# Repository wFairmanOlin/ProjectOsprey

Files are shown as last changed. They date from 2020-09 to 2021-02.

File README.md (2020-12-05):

# Project Osprey
#### Daniel Connolly and William Fairman

A Fall 2020 Project

<p align="center">
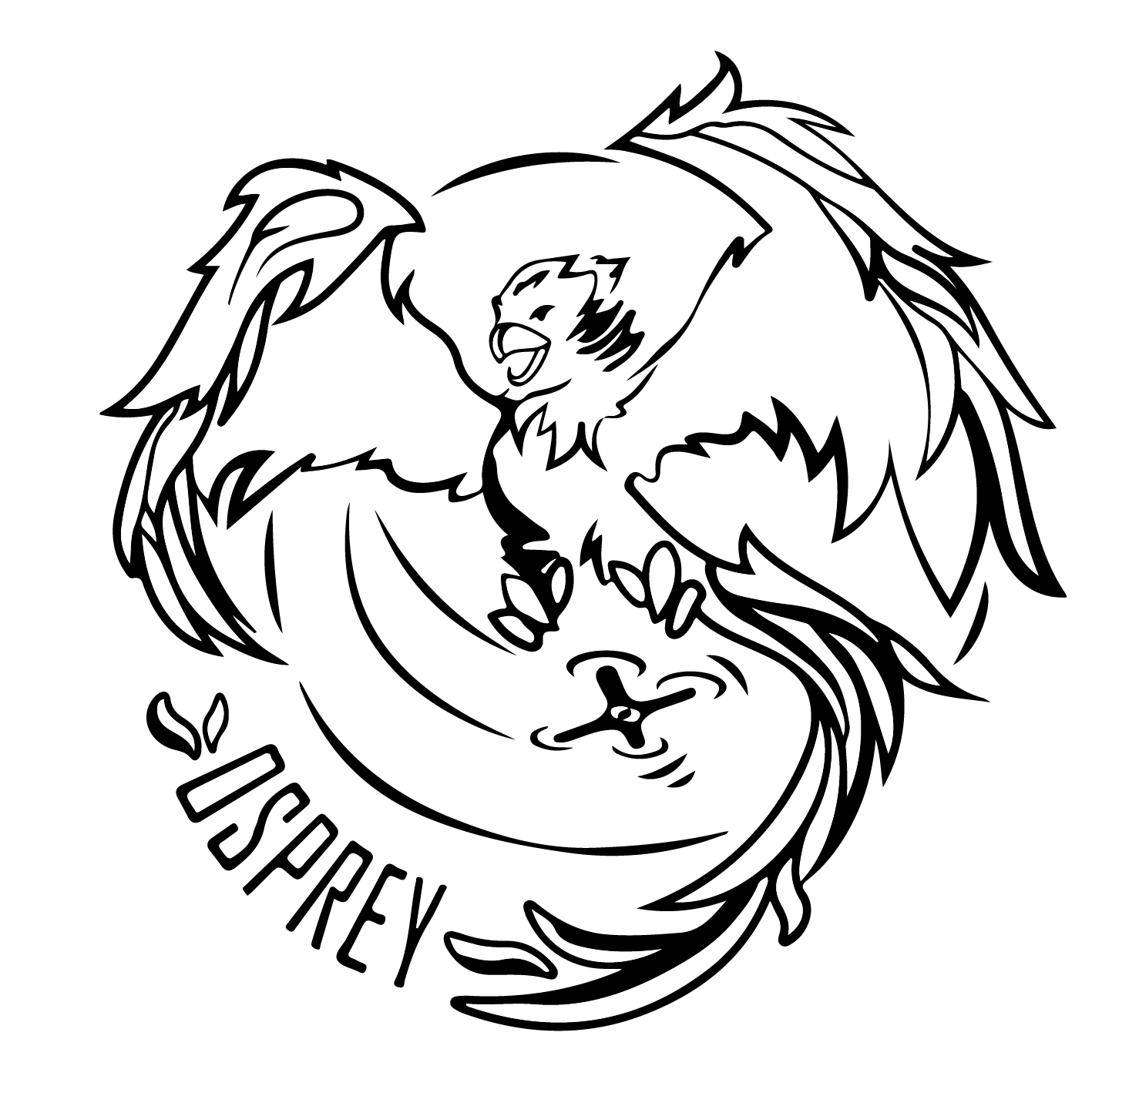
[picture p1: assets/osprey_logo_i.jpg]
Project Osprey

</p>
<p align="center">
<small>
<!--This logo is a modified version of work done by <a href="https://hweishin.carbonmade.com/">Hwei-Shin Harriman</a>, a fellow Olin student.--!>
  </small>
</p>

### Overview

We are developing a flight computer and drone as an exploration in electrical, mechanical, and firmware design.

### Subsystems

#### Electrical

Our flight computer is centered around the STM32F427VIT6 microcontroller. We have selected an IMU, barometer, GPS, and magnetometer to capture all of the necessary sensor data during flight. In addition, our board is equipped with a raspberry pi zero to which we intend to connect a small camera; the raspi communicates with the STM32 via I2C. We are also including a variety of connectors based off the [pixhawk design standard](https://github.com/pixhawk/Pixhawk-Standards/blob/master/DS-009%20Pixhawk%20Connector%20Standard.pdf) in order to connect to a variety of radios (FrSky, Spektrum, telemetry modules, etc). In order to be compatible with PX4 software, our computer also contains a microSD slot and on-board flash storage. Finally, we have created a power management system based around a TI buck converter that steps down battery voltage (12-25V) to 5V. Additional low-dropout regulators have been added to provided noise-free 3V3 to the sensors, STM, and radio modules. 

Besides providing basic computer vision, we are intending on utilizing the wifi chip on the raspi to stream video over a local network.

##### PCB Design
We have designed the first revision of our flight computer using Kicad and are currently waiting for fabrication and assembly from PCBWay. The board is 4 layers (Signal, GND, VCC, Signal) and contains roughly 120 surface mounted components. The minimnum trace/spacing width is 10/10mil.

![pcb_3d_view](assets/pcb_3d_view.png)

We have already been thinking about a revision 2! Heres what might be in the pipeline:
1. Onboard 2.4ghz radio (with a pcb antennae)
2. Replacing raspi with STM32H-series chip (embedded neural nets)
3. Faster primary micro-controller
4. Shrinking layout by replacing 0805 footprints with 0603 or smaller.

#### Mechanical

We are creating a 3-D printable chassis for our drone in AutoDesk's Fusion 360. At the moment, we are experimenting with Fusion 360's generative design features and how well these designs perform when 3-D printed as well as creating the basic chassis layout.

#### Firmware / Software

While we have not yet begun firmware / software development, we intend to start once we have shipped version 1 of our PCB. We expect to work in C++/C while developing for the STM32 as well as Python as we develop software on the raspberry pi.

### Goals

Our overarching goal for this project is to develop a drone capable of autonomous or semi-autonomous flight. In pursuit of this goal, we hope to advance our skills in the following areas:

1. Electrical design & PCB layout: This entails selecting the mcu, sensors, power management systems, and all supporting hardware as well as continuing to develop our KiCad knowledge.

2. Firmware development: We intend to learn C++ and advance our knowledge of firmware.

3. Computer vision: We have equipped our system with a raspberry pi with the intention of connecting a camera for basic computer vision processing.

4. Mechanical design: Taking high-level constraints about lift and drone layout into consideration, we intend to extend our CAD abilities.

Like the logo? This logo is a modified version of work done by [Hwei-Shin Harriman](https://hweishin.carbonmade.com/), a fellow Olin student.

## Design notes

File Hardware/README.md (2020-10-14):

# Project Osprey Electrical Hardware

We are designing a PCB in KiCad centered around an STM32 microcontroller for our flight computer.

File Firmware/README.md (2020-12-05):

# Project Osprey Firmware

We intend for our drone to fly semi-autonomously.

### TO DO:

- Look into Docker containerization of development environment
- Setup QGroundControl for use with our sensors
- Read through PX4 Firmware code
- Setup JMavSim and/or Gazebo for simulation

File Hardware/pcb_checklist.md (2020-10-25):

# PCB Checklist

## Review Parts (for new parts)
1. Check physical dimensions of fooptrint against datasheet 
2. Ensure pin numbers are properly oriented
3. Check num of pins on footprint and part-schematic
4. Ensure cathode/anode pin number is same on the datasheet, part-schematic, and footprint

## Review Schematic
1. Make sure all labels are connected and spelled correctly
2. Check GND and VDD connections
3. Ensure connectors are properly wired
3. Run DRC

## Review Layout
1. Check min tracing/spacing and vias match manufacturing specs
2. Check for overlapping fills (proper priorities set)
3. Look for fill islands (unconnected fills)
4. Make sure all text on Front/Back is visible
5. Make sure revision num, date, and author are up to date
6. Run 3D viewer to verify silkscreen
7. Run DRC

## Review Gerber
1. Check gerber output location for older files
2. Check centroid/drill locaiton for older files
3. Import gerber and drill files into Gerber Viewer (KiCad)

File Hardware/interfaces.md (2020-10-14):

## Interfaces
- SWD/JTAG
- Power (px)
  1. VCC_5V
  2. VCC_5V
  3. BATT_CURRENT
  4. BATT_VOLTAGE
  5. GND
  6. GND
- Power (4in1 ESC)
  1. VBAT
  2. TLM
  2. GND
  3. BATT_CURRENT
  4. M1
  5. M2
  6. M3
  7. M4
- SBUS
  1. VCC_5V
  2. SBUS
  3. RSSI
  4. VCC_3V3
  5. GND
- Telemetry
  1. VCC_5V
  2. MCU_TX
  3. MCU_RX
  4. MCU_CTS
  5. MCU_RTS
- PWM
- USB

### Optional
- DCMI
- SPI
- UART & I2C
- CAN
- PPM

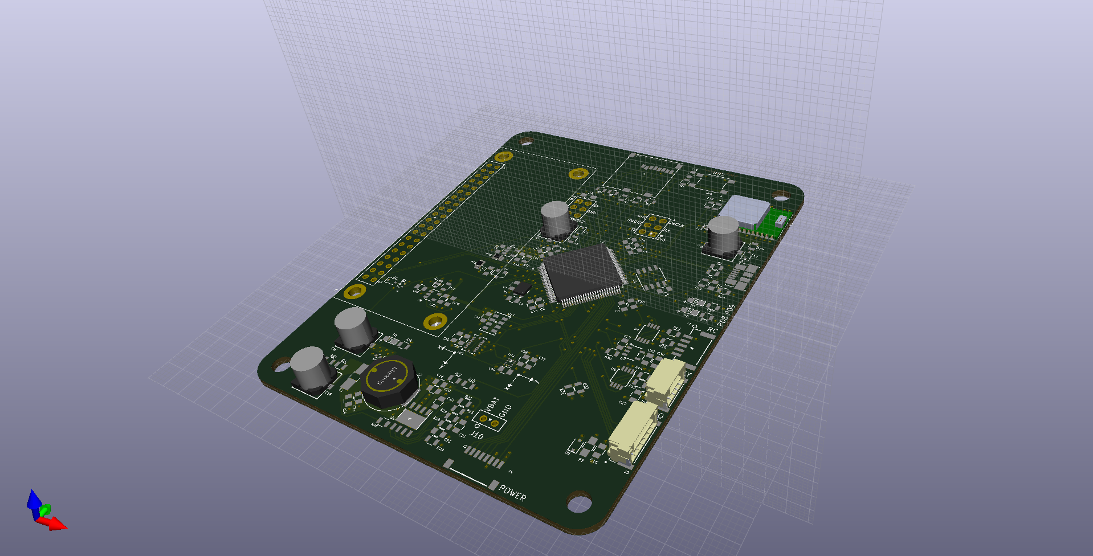
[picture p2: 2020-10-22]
Hardware/rev2/flight_computer/flight_computer.png

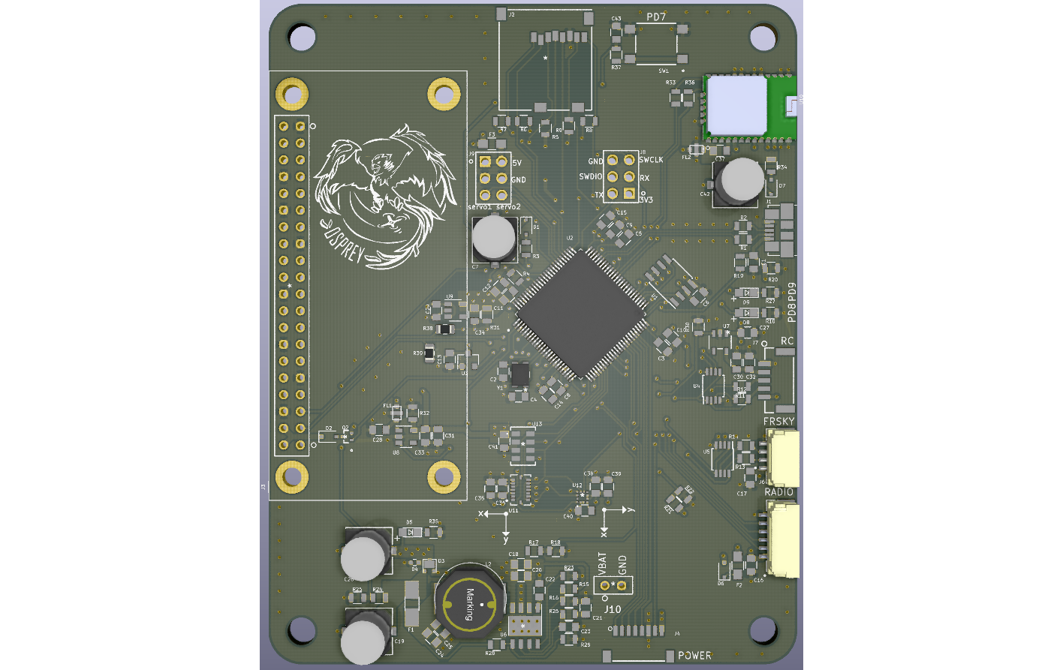
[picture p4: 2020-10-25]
assets/pcb_3d_view.png

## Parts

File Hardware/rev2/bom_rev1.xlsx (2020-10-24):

 |  |  | REV 1 BOM
Item # | *Designator | *Qty | Manufacturer | *Mfg Part # | Description / Value | *Package/Footprint | Type | Your Instructions / Notes
1 | C19, C26 | 2 | Rubycon | 10SGV100M6.3X6.1 | C_100u | SMD | SMD
2 | C21 | 1 | Murata Electronics | GRM2195C1H123GA01D | C_0u012 | 0805 | SMD
3 | C23 | 1 | Samsung Electro-Mechanics | CL21C121JDCNNNC | C_120P | 0805 | SMD
4 | C24, C25 | 2 | Taiyo Yuden | JMK212BJ476MG-T | C_47u | 0805 | SMD
5 | C37 | 1 | Murata Electronics | GRM21BR71C475KE51L | C_4u7 | 0805 | SMD
6 | C38 | 1 | KEMET | C0805C105Z4VACTU | C_1u | 0805 | SMD
7 | C4, C2 | 2 | Yageo | CC0805DRNPO9BN8R0 | C_8p | 0805 | SMD
8 | C43, C18, C34, C33, C27, C30 | 6 | Murata Electronics | GRM21BR61E106KA73K | C_10u | 0805 | SMD
9 | C6, C10, C11, C12, C14, C15, C13, C1, C20, C22, C31, C32, C36, C40, C39, C41, C35 | 17 | AVX Corporation | 08055C104JAT2A | C_0u1 | 0805 | SMD
10 | C7, C42 | 2 | Nichicon | UWT0G221MCL6GS | C_220u | SMD | SMD
11 | C9, C8, C3, C5, C16, C17, C29, C28 | 8 | TDK Corporation | CGB4B1X6S1C225K055AC | C_2u2 | 0805 | SMD
12 | D2, D1, D6, D7 | 4 | Nexperia USA Inc. | PMEG1030EJ,115 | D_Schottky_10V_3A | D_SOD-323F | SMD
13 | D3 | 1 | Nexperia USA Inc. | PMEG2020CPA,115 | D_Schottky_x2_20V | SOT1061 | SMD
14 | D4 | 1 | Littelfuse Inc. | PESD0402-140 | TVS_DIODE_14V | 0402 | SMD
15 | D8, D5 | 2 | OSRAM Opto Semiconductors Inc. | LG R971-KN-1 | LED_0805_Green | 0805 | SMD
16 | D9 | 1 | OSRAM Opto Semiconductors Inc. | LG R976-NR-1 | LED_0805_Red | 0805 | SMD
17 | F1 | 1 | Bel Fuse Inc. | 0ZCJ0200FF2C | PTC_6V_2A | 1206 | SMD
18 | F2, F3 | 2 | Bel Fuse Inc. | 0ZCK0050FF2E | PTC_6V_1A | 0805 | SMD
19 | FL1, FL2 | 2 | Murata Electronics | NFL21SP107X1C3D | EMI_Filter_CLC_100MHZ | SMD | SMD
20 | J1 | 1 | Molex | 473460001 | Micro_USB | SMD | SMD
21 | J10 | 1 | N/A | N/A | N/A | N/A | DNS | ignore part
22 | J2 | 1 | 3M | 2908-05WB-MG | MicroSD_molex | SMD | SMD
23 | J3 | 1 | N/A | N/A | N/A | N/A | DNS | ignore part
24 | J4 | 1 | JST Sales America Inc. | SM08B-SRSS-TB(LF)(SN) | JST_8_RA | SMD | SMD
25 | J5 | 1 | JST Sales America Inc. | SM06B-GHS-TB(LF)(SN) | JST_GH_6_RA | SMD | SMD
26 | J6 | 1 | JST Sales America Inc. | SM04B-GHS-TB(LF)(SN)- | JST_GH_4_RA | SMD | SMD
27 | J7 | 1 | JST Sales America Inc. | SM05B-GHS-TB(LF)(SN) | JST_GH_5_RA | SMD | SMD
28 | J8, J9 | 2 | Samtec Inc. | TSW-103-07-F-D | Conn_02x03 | through hole | through hole
29 | L2 | 1 | Würth Elektronik | 744066150 | L_15u | SMD | SMD
30 | Q2 | 1 | ON Semiconductor | NTA4151PT1G | PMOS_20V_.76A | SMD | SMD
31 | R1, R2 | 2 | Bourns Inc. | CR0805-FX-22R0ELF | R_22 | 0805 | SMD
32 | R10, R27 | 2 | Stackpole Electronics Inc | RMCF0805FT51R1 | R_51.1 | 0805 | SMD
33 | R12, R20 | 2 | TE Connectivity Passive Product | CRGCQ0805F470R | R_470 | 0805 | SMD
34 | R15, R31, R32, R25, R24, R36, R33 | 7 | Yageo | RC0805FR-07220RL | R_220 | 0805 | SMD
35 | R16 | 1 | Yageo | RC0805FR-0743K2L | R_43K2 | 0805 | SMD
36 | R17 | 1 | Yageo | RC0805FR-0769K8L | R_69K8 | 0805 | SMD
37 | R23 | 1 | Stackpole Electronics Inc | RMCF0805FT143K | R_143K | 0805 | SMD
38 | R26 | 1 | Stackpole Electronics Inc | RMCF0805FT3K74 | R_3K74 | 0805 | SMD
39 | R29 | 1 | Vishay Dale | CRCW080519K1FKEA | R_19K1 | 0805 | SMD
40 | R3, R13, R14, R34 | 4 | Yageo | RC0805JR-071KL | R_1K | 0805 | SMD
41 | R35 | 1 | TE Connectivity Passive Product | CRGCQ0805F120R | R_120 | 0805 | SMD
42 | R39, R38 | 2 | Yageo | RC0805FR-0710KL | R_10K | 0805 | SMD
43 | R4, R37, R11, R30, R19, R22, R21, R18 | 8 | Yageo | RC0805FR-07100KL | R_10K | 0805 | SMD
44 | R9, R8, R7, R6, R5, R28 | 6 | Stackpole Electronics Inc | RMCF0805JT68R0 | R_100K | 0805 | SMD
45 | SW1 | 1 | C&K | PTS645SM43SMTR92 LFS | Switch_SMT | SMD | SMD
46 | U1 | 1 | Cypress Semiconductor Corp | FM25V01A-G | FRAM_128K | SOIC-8 | SMD
47 | U10 | 1 | U-Blox | CAM-M8Q-0 | CAM-M8Q-0 | SMD | SMD
48 | U11 | 1 | Bosch Sensortec | BMI088 | BMI088 | SMD | SMD
49 | U12 | 1 | STMicroelectronics | LIS3MDLTR | LIS3MDLTR | SMD | SMD
50 | U13 | 1 | TE Connectivity Measurement Specialties | MS561101BA03-50 | Barometer | SMD | SMD
51 | U2 | 1 | STMicroelectronics | STM32F427VIT6 | STM32F427VITx | SMD | SMD
52 | U3 | 1 | Microchip Technology | MCP131T-300E/TT | MCP131T-300E_TT | SOT-23 | SMD
53 | U5, U4 | 2 | Nexperia USA Inc. | 74LVC2G86DP,125 | Dual_XOR_GATE | TSSOP-8 | SMD
54 | U6 | 1 | Texas Instruments | TPS54335ADDA | Buck_Converter_2 | SMD | SMD
55 | U7 | 1 | Diodes Incorporated | AP7365-33WG-7 | LDO_600MA | SOT-25_DIO | SMD
56 | U9, U8 | 2 | Texas Instruments | LP5907QMFX-3.3Q1 | LP5907QMFX-3.3 | SOT-23-5 | SMD
57 | Y1 | 1 | NDK America, Inc. | NX3225SA-24.000M-STD-CSR-1 | Crystal_24MHZ | SMD | SMD

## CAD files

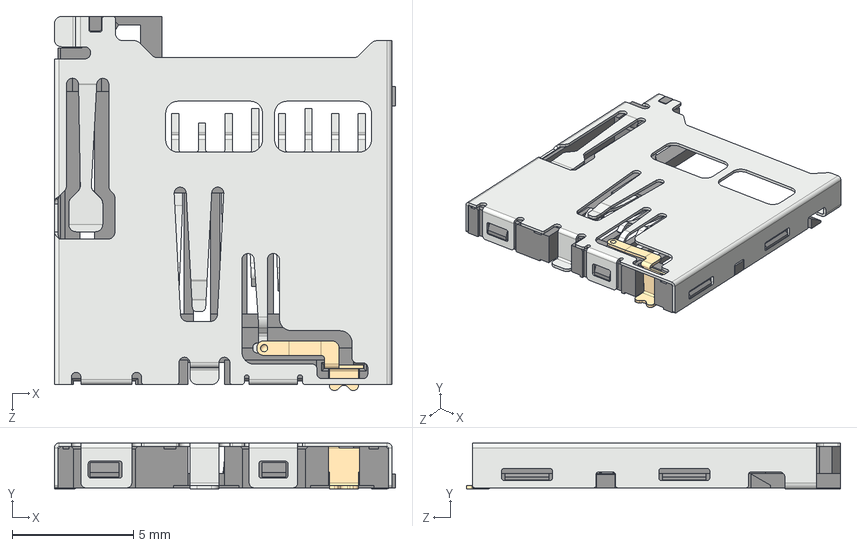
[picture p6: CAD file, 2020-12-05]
Hardware/3D_parts/micro SD Card Slot.step
14.1 x 1.90 x 15.5 mm
microSD_Body
microSD_Cover
microSD_Card_Detect
microSD_Pin_11.15 x 5
microSD_Pin_11.35 x 2
microSD_Pin_10.75

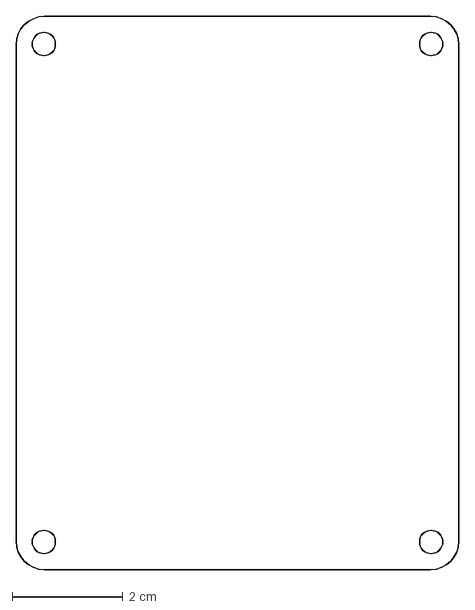
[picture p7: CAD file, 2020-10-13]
Hardware/rev2/flight_computer/circuitBoard v2.dxf
8.00 x 10.0 cm

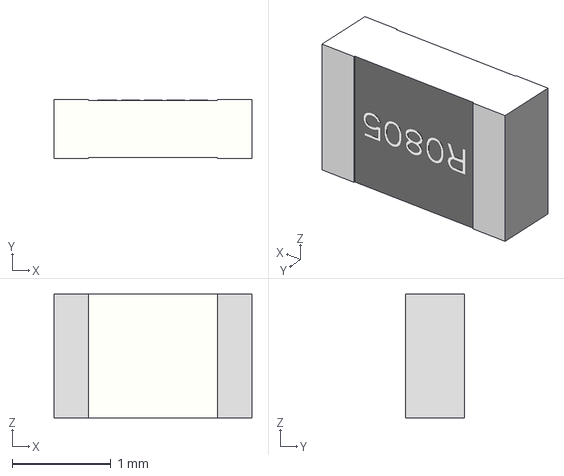
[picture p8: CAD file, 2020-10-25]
Hardware/3D_parts/rsmd-0805_l2_w1-25_h0-6.stp
2.00 x 0.6 x 1.25 mm

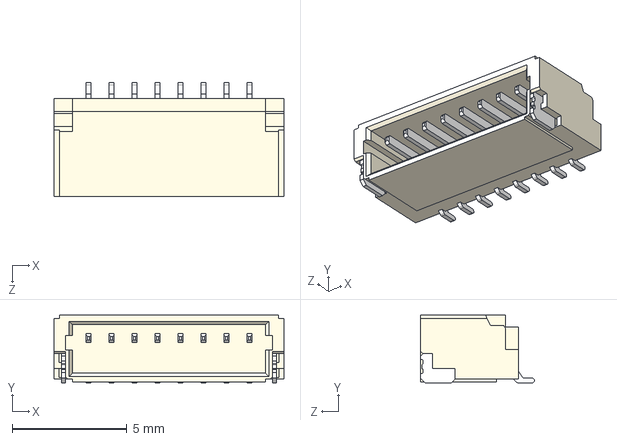
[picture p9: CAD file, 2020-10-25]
Hardware/3D_parts/SM08B-SRSS-TB(LF)(SN)--3DModel-STEP-56544.STEP
10.00 x 2.95 x 4.95 mm

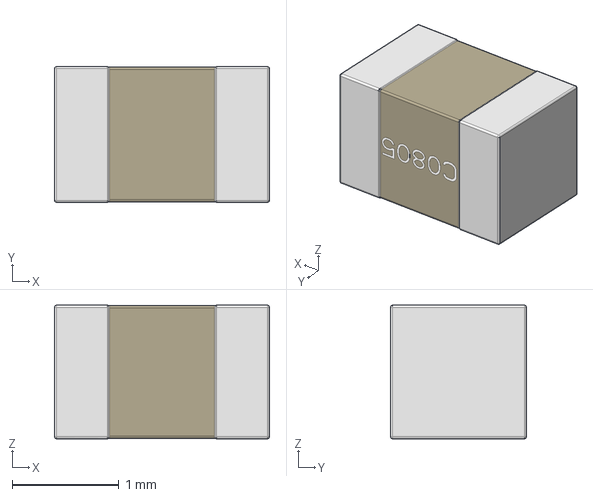
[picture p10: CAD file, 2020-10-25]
Hardware/3D_parts/csmd-0805_l2-01_w1-25_h1-27.stp
2.01 x 1.27 x 1.25 mm

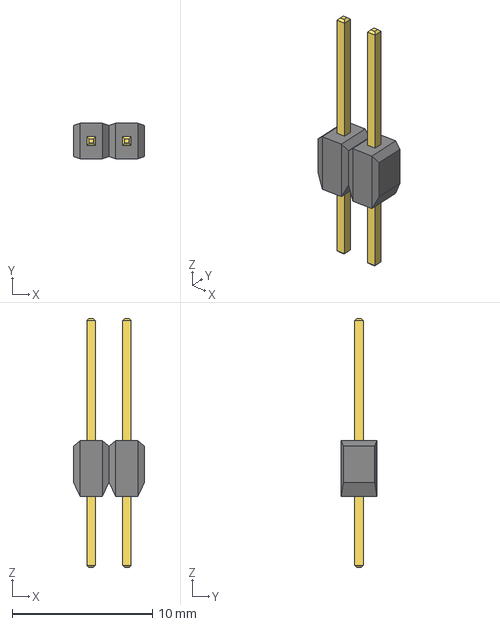
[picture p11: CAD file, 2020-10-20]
Hardware/3D_parts/CON2_1X2_TU_TSW.step
5.08 x 2.54 x 17.8 mm

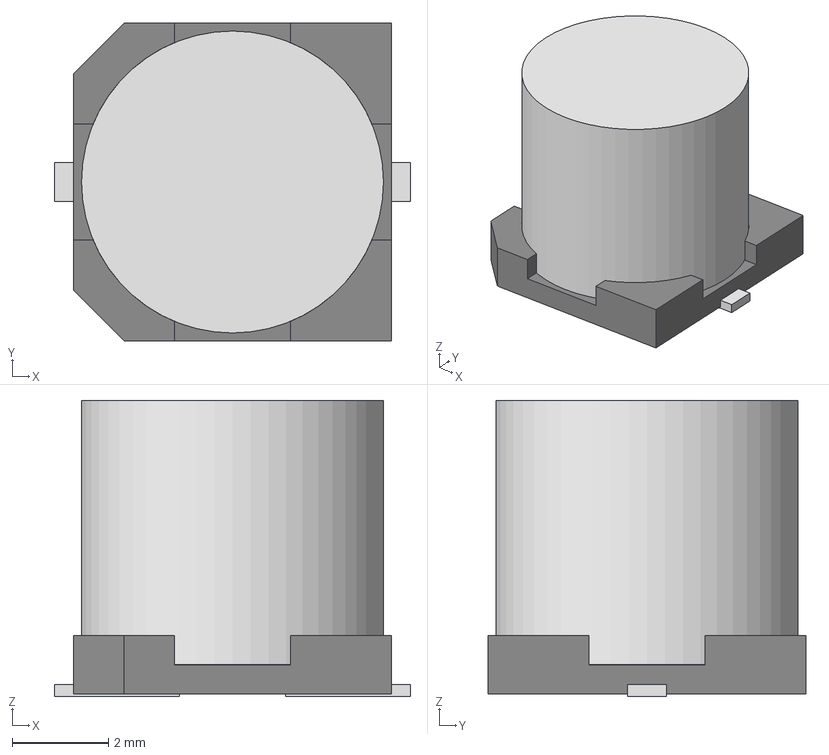
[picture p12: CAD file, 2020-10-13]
Hardware/3D_parts/CAP_UCD_6P3X5P8_NCH.step
7.39 x 6.60 x 6.15 mm

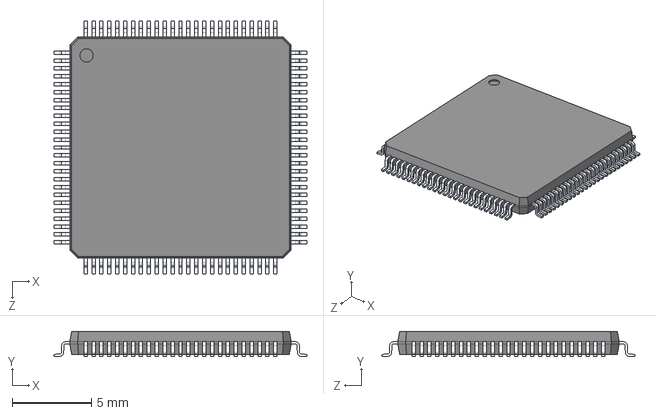
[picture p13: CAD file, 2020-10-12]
Hardware/3D_parts/STM32F427VIT6.STEP
16.0 x 1.60 x 16.0 mm

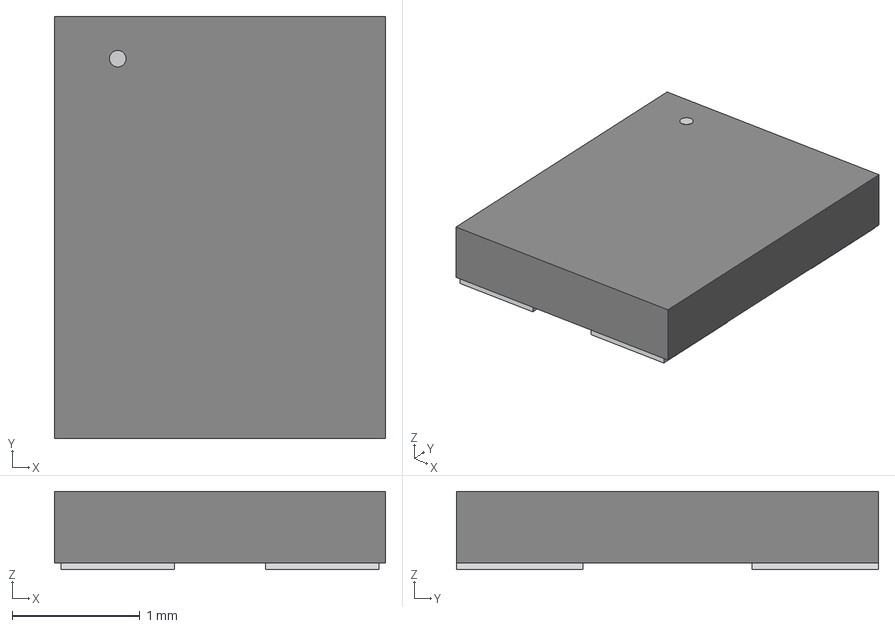
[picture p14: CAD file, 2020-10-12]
Hardware/3D_parts/NX3225SA-24_000M-STD-CSR-1_NDK.step
2.59 x 3.30 x 0.612 mm

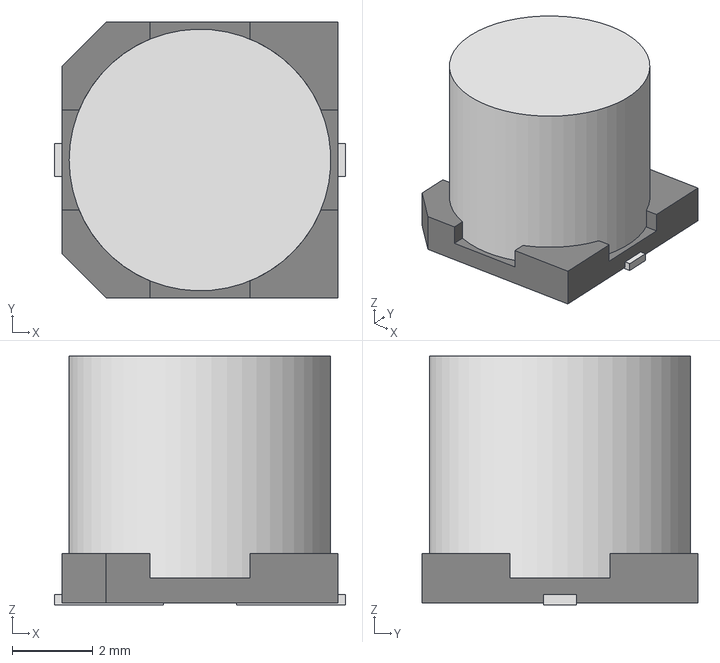
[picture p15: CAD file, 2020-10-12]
Hardware/3D_parts/CAP_J-V_6P3X6P1_RUB.step
7.19 x 6.81 x 6.15 mm

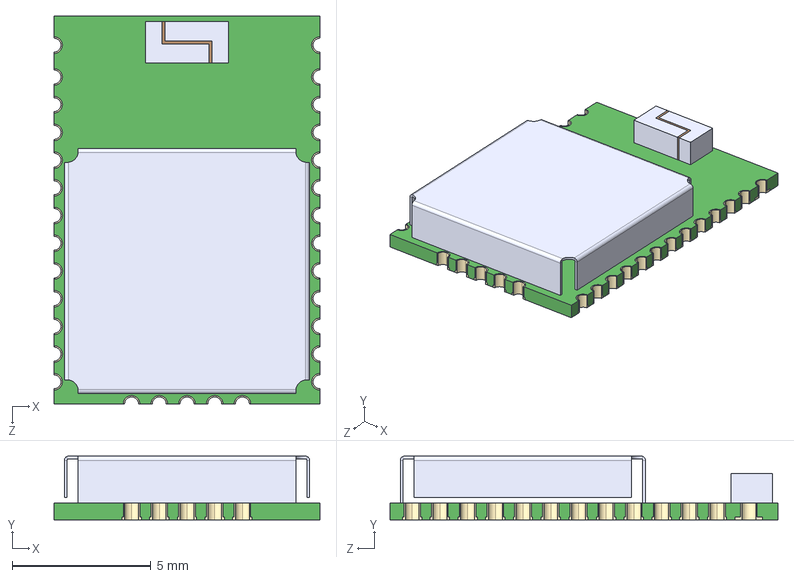
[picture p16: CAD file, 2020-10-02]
Hardware/3D_parts/CAM-M8Q-0--3DModel-STEP-56544.STEP
9.60 x 2.30 x 14.0 mm

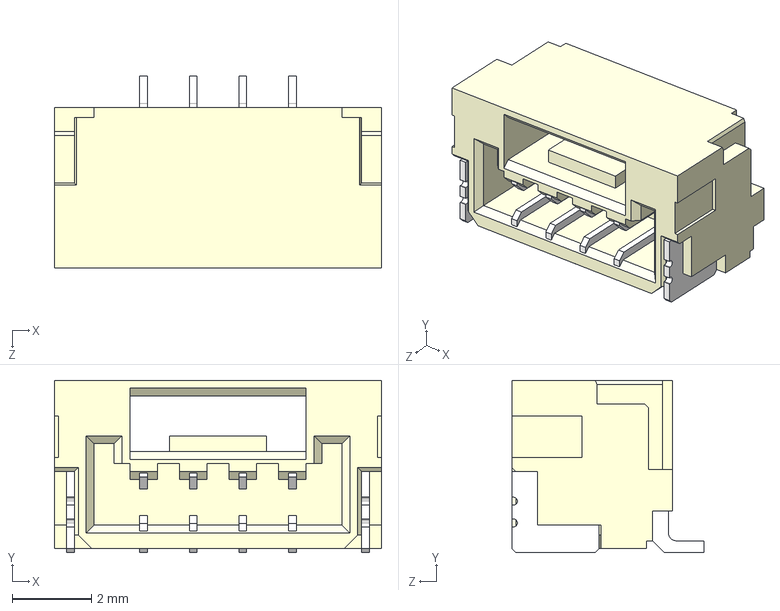
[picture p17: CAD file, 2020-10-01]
Hardware/3D_parts/SM04B-GHS-TB(LF)(SN)---3DModel-STEP-56544.STEP
8.25 x 4.35 x 4.85 mm

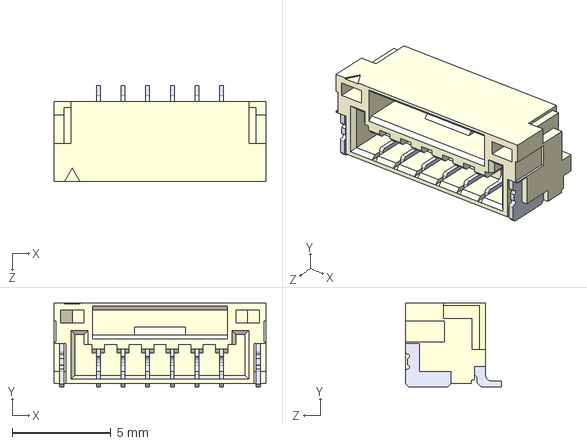
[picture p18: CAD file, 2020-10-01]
Hardware/3D_parts/SM06B-GHS-TB(LF)(SN)--3DModel-STEP-56544.STEP
10.8 x 4.25 x 4.85 mm

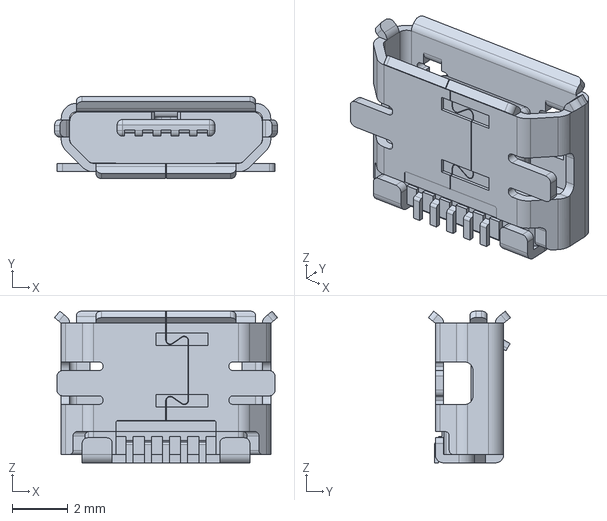
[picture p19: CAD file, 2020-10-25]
Hardware/3D_parts/473460001.stp
7.98 x 2.94 x 5.43 mm

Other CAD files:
Hardware/3D_parts/744066005_Download_STP_WE-TPC-1038_rev1.stp
Hardware/rev2/flight_computer/circuitBoard v1.dxf
Hardware/3d_flight_computer/flight_computer v1.f3d
Hardware/3d_flight_computer/flight_computer_stripped v3.f3d

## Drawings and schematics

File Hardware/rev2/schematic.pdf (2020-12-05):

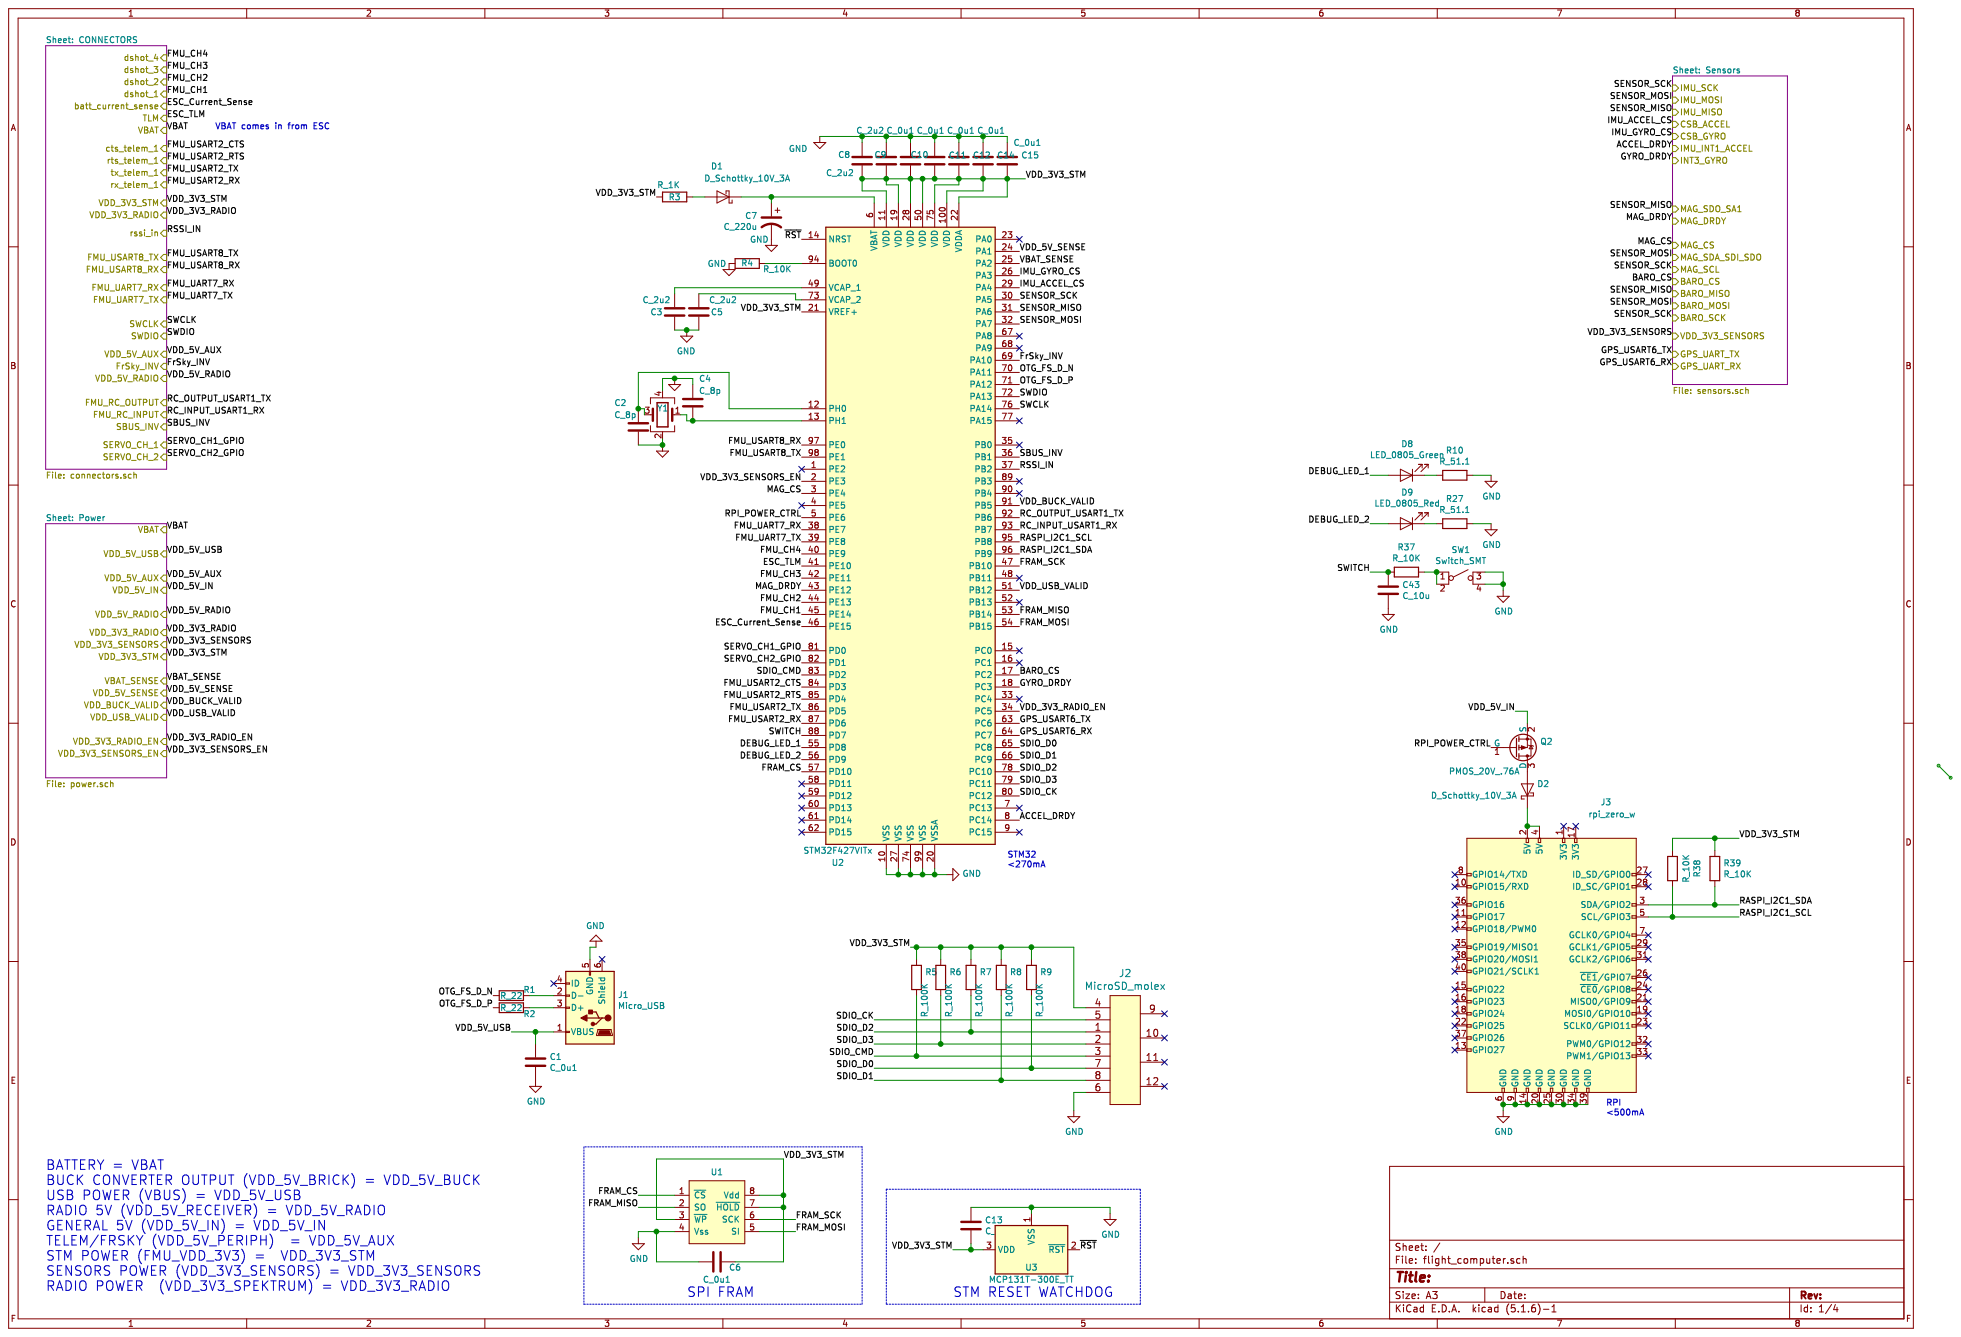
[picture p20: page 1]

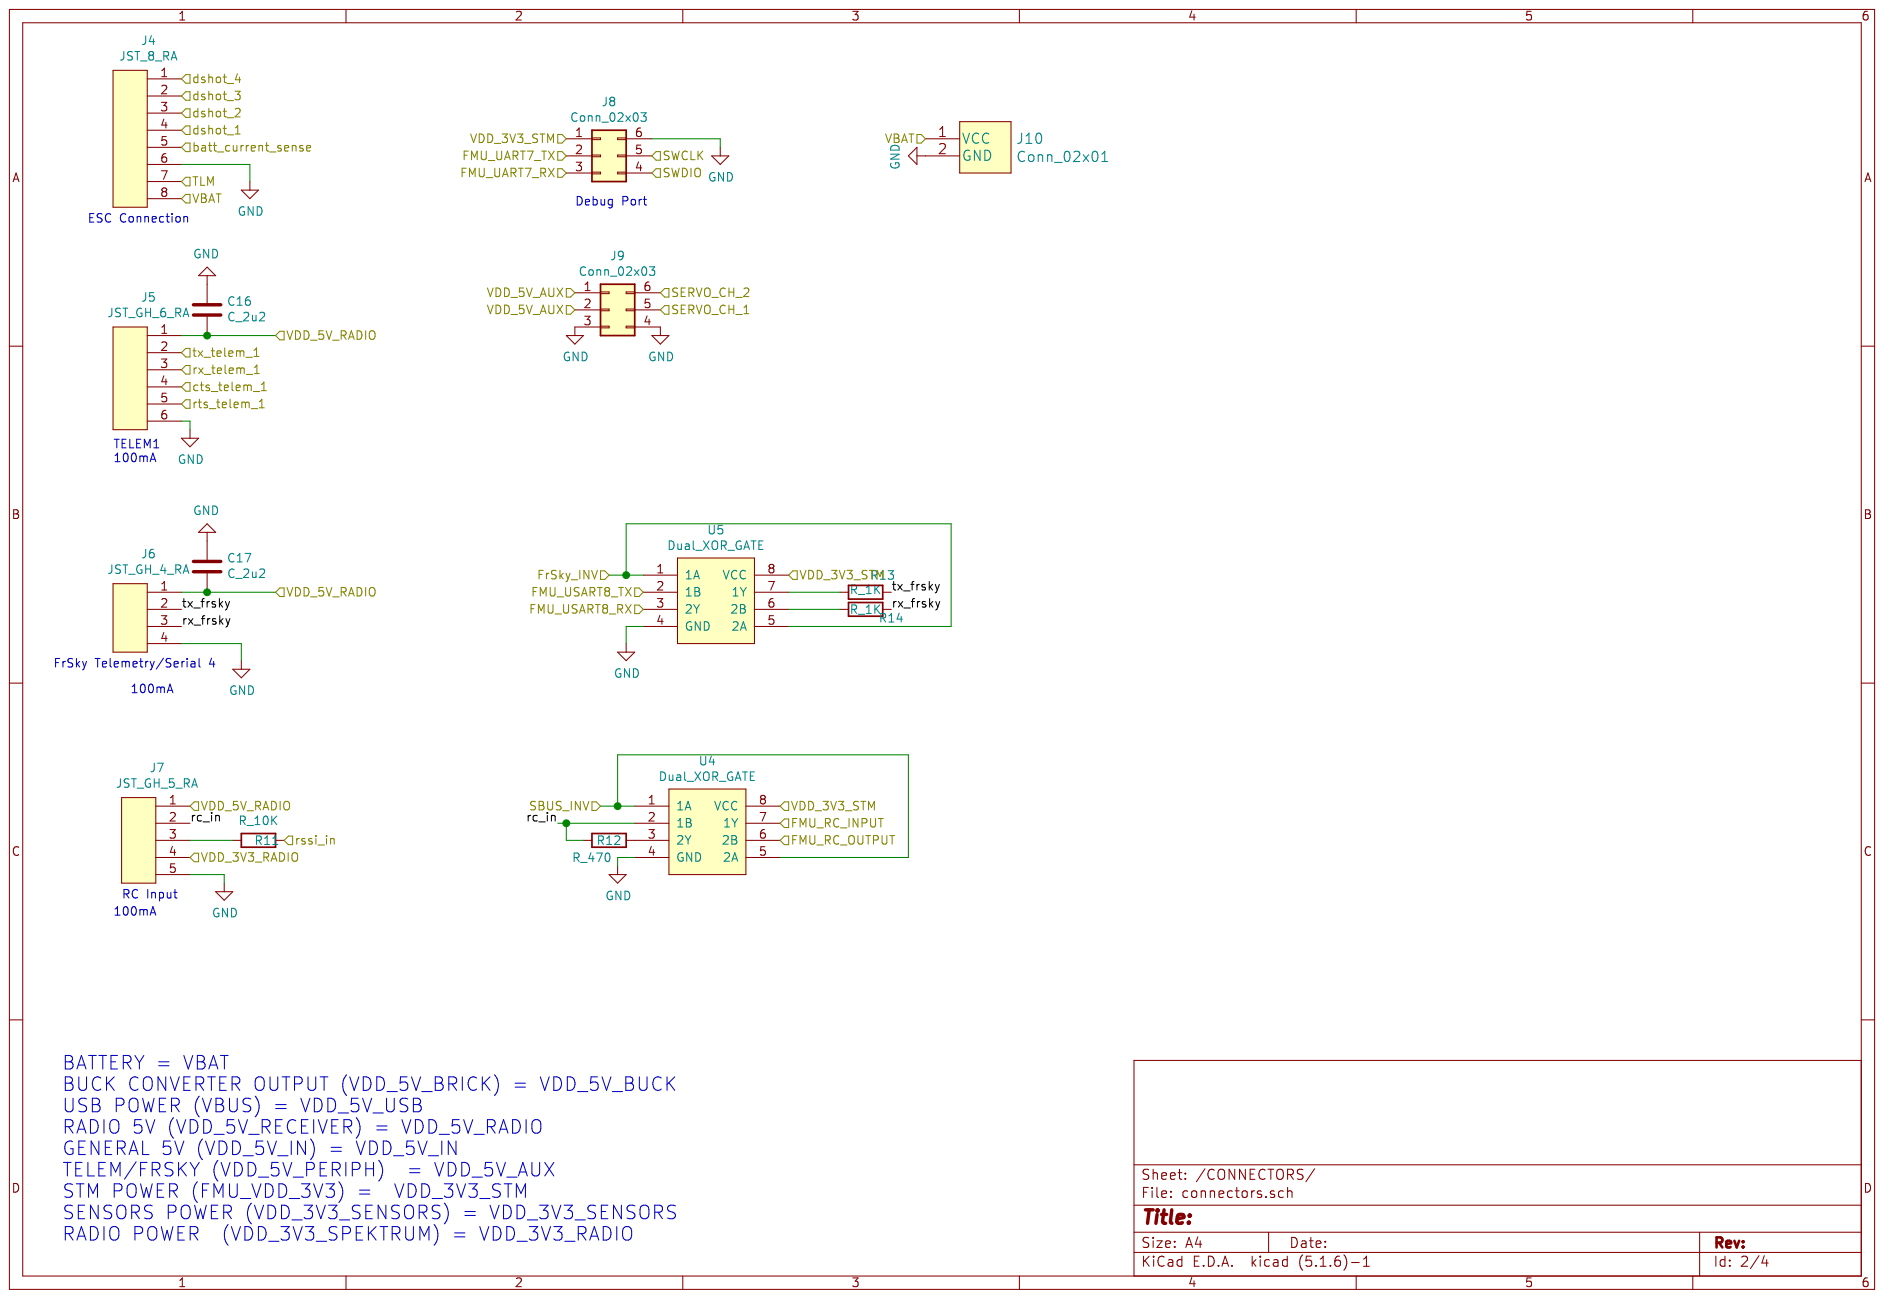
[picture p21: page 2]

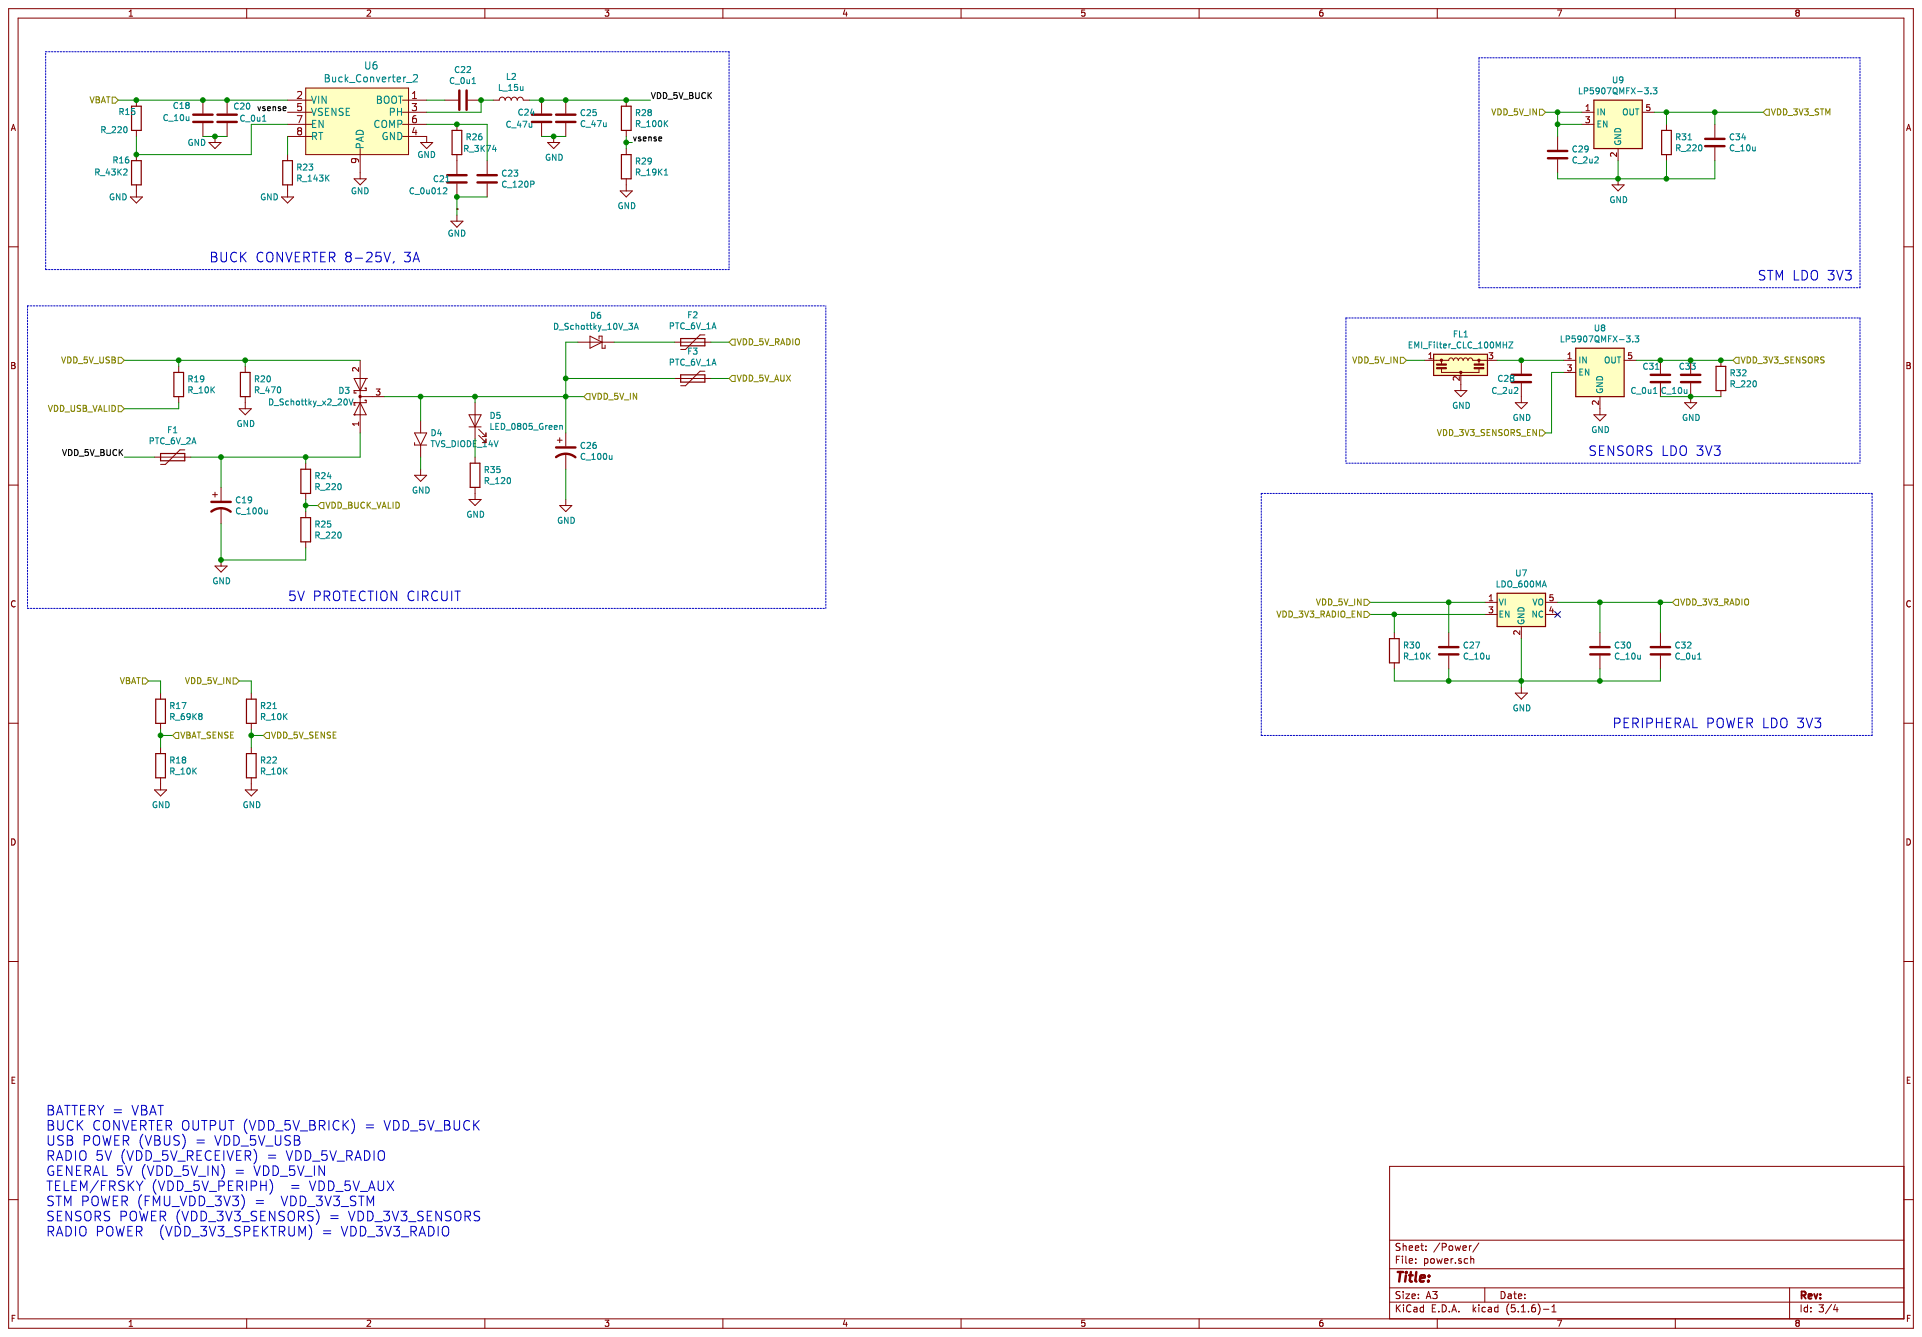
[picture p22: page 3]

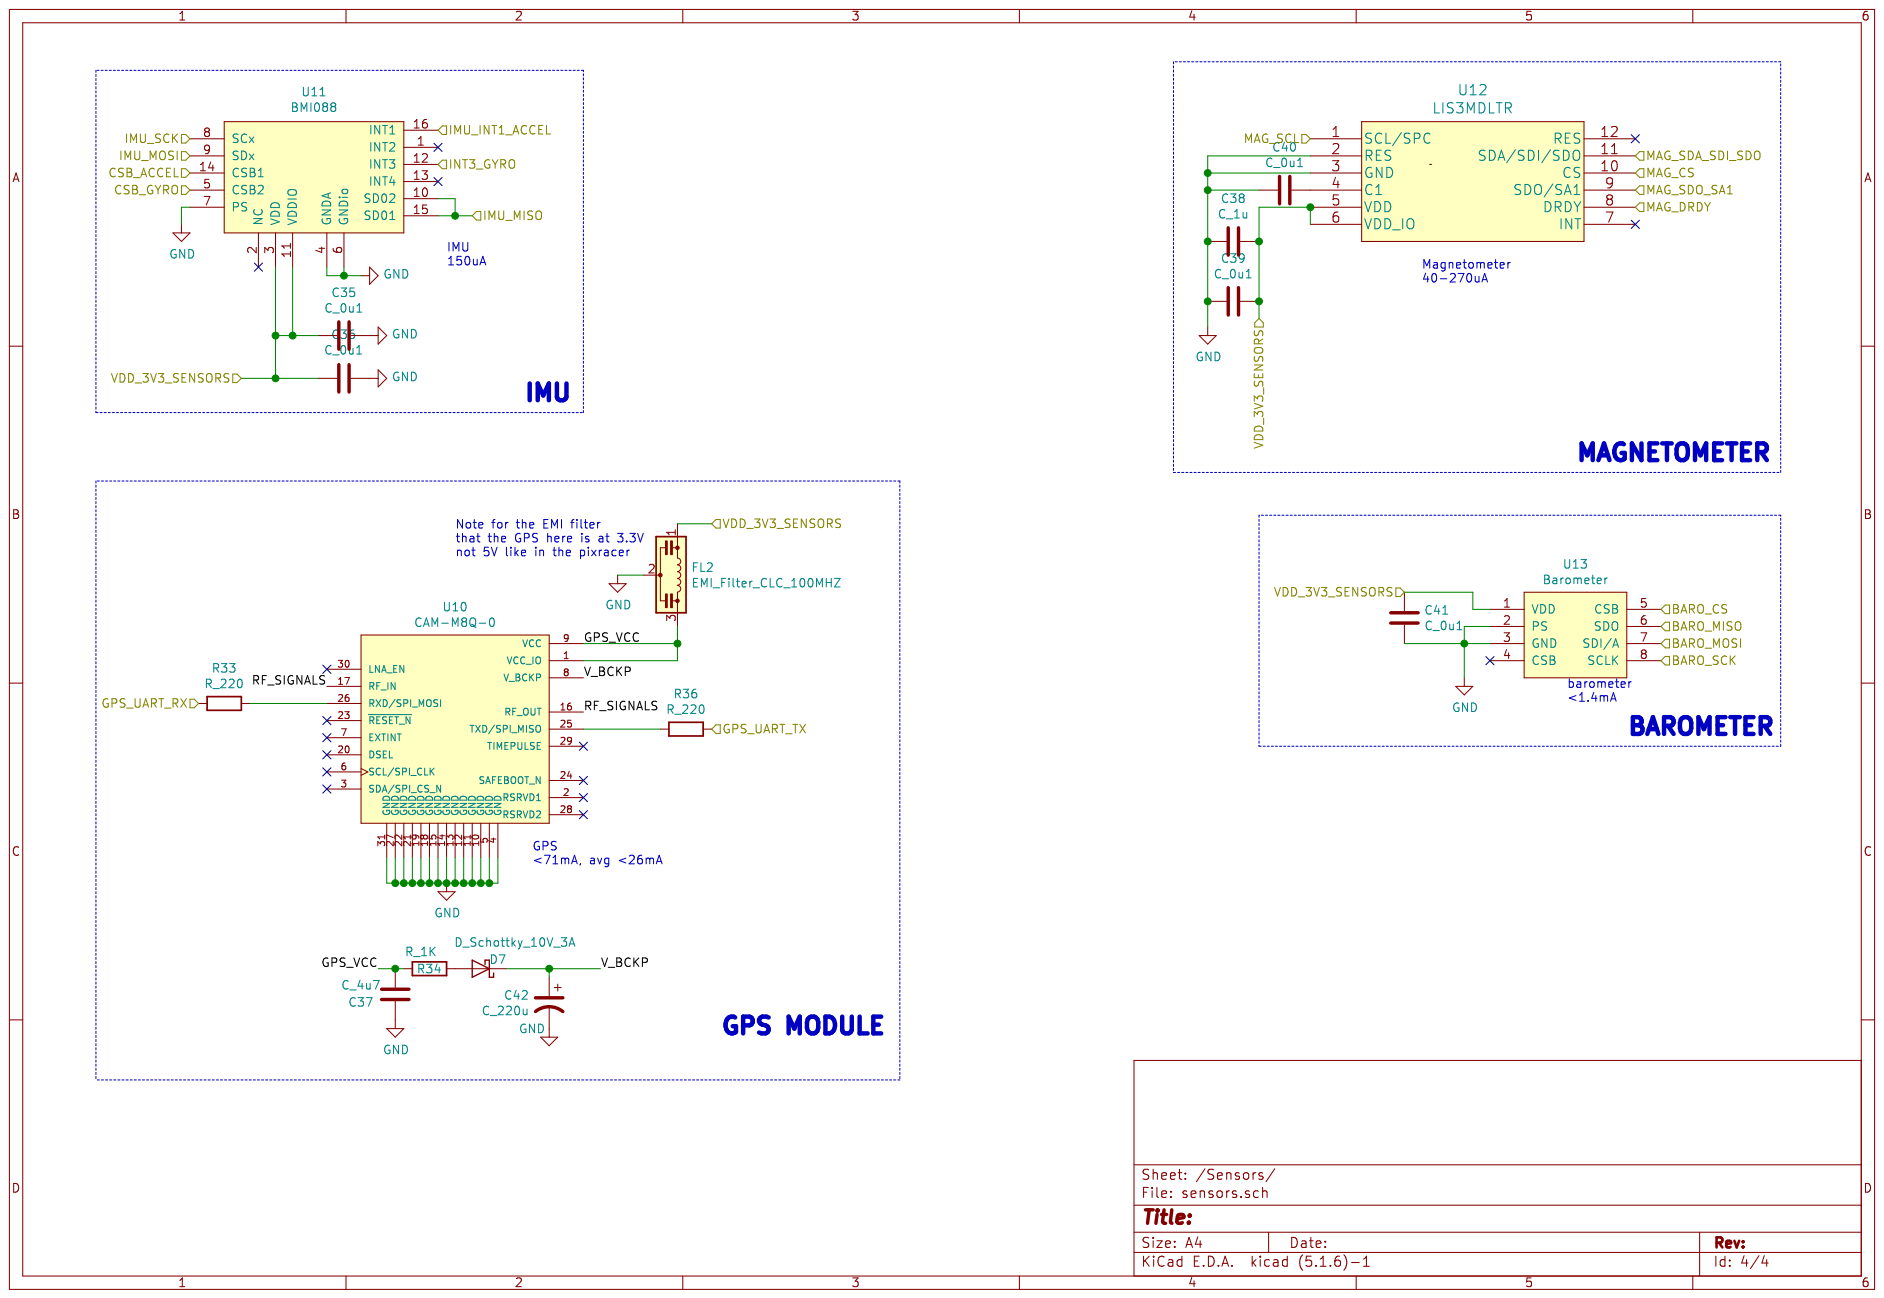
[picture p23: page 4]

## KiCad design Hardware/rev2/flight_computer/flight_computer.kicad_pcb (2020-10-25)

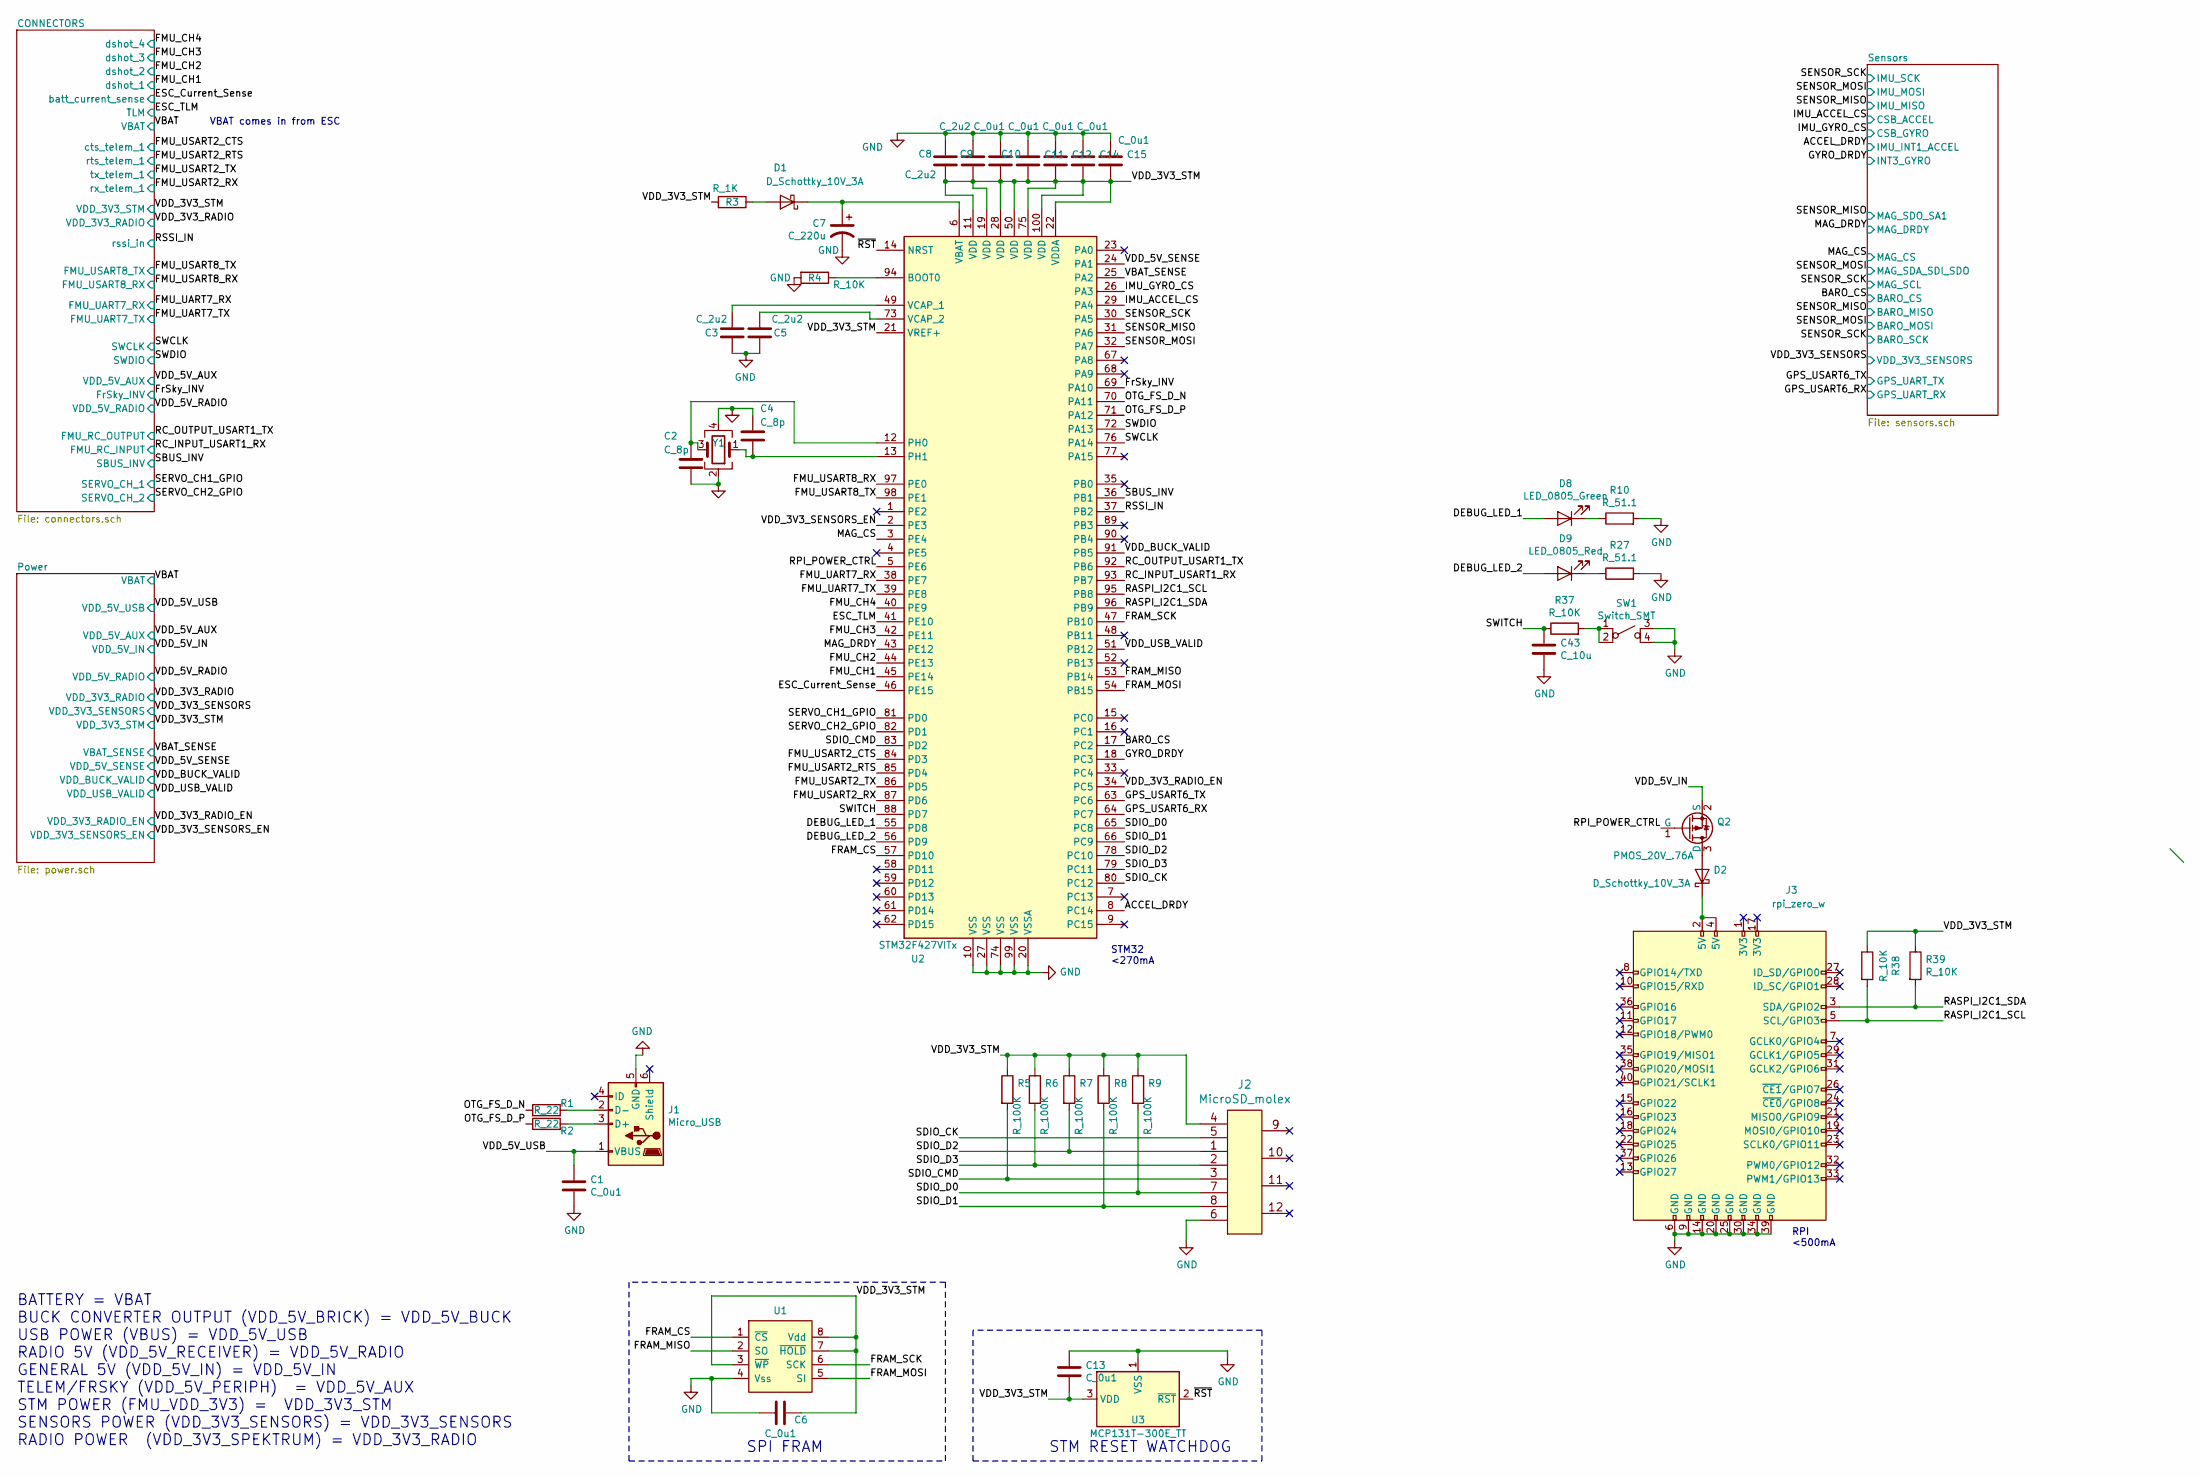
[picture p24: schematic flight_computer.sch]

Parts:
C1, C6, C10, C11, C12, C13, C14, C15: C_0u1; C_0805
C2, C4: C_8p; C_0805
C3, C5, C8, C9: C_2u2; C_0805
C7: C_220u; UWT0G221MCL6GS; MPN UWT0G221MCL6GS
C43: C_10u; C_0805
D1, D2: D_Schottky_10V_3A; D_SOD-323F; MPN PMEG1030EJ,115
D8: LED_0805_Green; LED_0805; MPN LG R971-KN-1
D9: LED_0805_Red; LED_0805; MPN LG R976-NR-1
J1: Micro_USB; MOLEX_0473460001
J2: MicroSD_molex; 2908-05WB-MG; MPN 2908-05WB-MG
J3: rpi_zero_w
Q2: PMOS_20V_.76A; NTA4151PT1G; MPN NTA4151PT1G
R1, R2: R_22; R_0805; MPN CR0805-FX-22R0ELF
R3: R_1K; R_0805
R4, R37, R38, R39: R_10K; R_0805
R5, R6, R7, R8, R9: R_100K; R_0805
R10, R27: R_51.1; R_0805; MPN RMCF0805FT51R1
SW1: Switch_SMT; PTS645SM43SMTR92LFS; MPN PTS645SM43SMTR92 LFS
U1: FRAM_128K; SOIC-8_3.9x4.9mm_Pitch1.27mm
U2: STM32F427VITx; LQFP-100_14x14mm_P0.5mm
U3: MCP131T-300E_TT; SOT-23
Y1: Crystal_24MHZ; NX3225SA-24.000M-STD-CSR-1; MPN NX3225SA-24.000M-STD-CSR-1

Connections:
/ACCEL_DRDY: U2.8 (PC14); also elsewhere on the board
/BARO_CS: U2.17 (PC2); also elsewhere on the board
/DEBUG_LED_1: D8.2 (A), U2.55 (PD8)
/DEBUG_LED_2: D9.2 (A), U2.56 (PD9)
/ESC_Current_Sense: U2.46 (PE15); also elsewhere on the board
/ESC_TLM: U2.41 (PE10); also elsewhere on the board
/FMU_CH1: U2.45 (PE14); also elsewhere on the board
/FMU_CH2: U2.44 (PE13); also elsewhere on the board
/FMU_CH3: U2.42 (PE11); also elsewhere on the board
/FMU_CH4: U2.40 (PE9); also elsewhere on the board
/FMU_UART7_RX: U2.38 (PE7); also elsewhere on the board
/FMU_UART7_TX: U2.39 (PE8); also elsewhere on the board
/FMU_USART2_CTS: U2.84 (PD3); also elsewhere on the board
/FMU_USART2_RTS: U2.85 (PD4); also elsewhere on the board
/FMU_USART2_RX: U2.87 (PD6); also elsewhere on the board
/FMU_USART2_TX: U2.86 (PD5); also elsewhere on the board
/FMU_USART8_RX: U2.97 (PE0); also elsewhere on the board
/FMU_USART8_TX: U2.98 (PE1); also elsewhere on the board
/FRAM_CS: U1.1 (~CS), U2.57 (PD10)
/FRAM_MISO: U1.2 (SO), U2.53 (PB14)
/FRAM_MOSI: U1.5 (SI), U2.54 (PB15)
/FRAM_SCK: U1.6 (SCK), U2.47 (PB10)
/FrSky_INV: U2.69 (PA10); also elsewhere on the board
/GPS_USART6_RX: U2.64 (PC7); also elsewhere on the board
/GPS_USART6_TX: U2.63 (PC6); also elsewhere on the board
/GYRO_DRDY: U2.18 (PC3); also elsewhere on the board
/IMU_ACCEL_CS: U2.29 (PA4); also elsewhere on the board
/IMU_GYRO_CS: U2.26 (PA3); also elsewhere on the board
/MAG_CS: U2.3 (PE4); also elsewhere on the board
/MAG_DRDY: U2.43 (PE12); also elsewhere on the board
/OTG_FS_D_N: R1.1, U2.70 (PA11)
/OTG_FS_D_P: R2.1, U2.71 (PA12)
/RASPI_I2C1_SCL: J3.5 (SCL/GPIO3), R38.2, U2.95 (PB8)
/RASPI_I2C1_SDA: J3.3 (SDA/GPIO2), R39.2, U2.96 (PB9)
/RC_INPUT_USART1_RX: U2.93 (PB7); also elsewhere on the board
/RC_OUTPUT_USART1_TX: U2.92 (PB6); also elsewhere on the board
/RPI_POWER_CTRL: Q2.1 (G), U2.5 (PE6)
/RSSI_IN: U2.37 (PB2); also elsewhere on the board
/SBUS_INV: U2.36 (PB1); also elsewhere on the board
/SDIO_CK: J2.5, U2.80 (PC12)
/SDIO_CMD: J2.3, R5.2, U2.83 (PD2)
/SDIO_D0: J2.7, R9.2, U2.65 (PC8)
/SDIO_D1: J2.8, R8.2, U2.66 (PC9)
/SDIO_D2: J2.1, R7.2, U2.78 (PC10)
/SDIO_D3: J2.2, R6.2, U2.79 (PC11)
/SENSOR_MISO: U2.31 (PA6); also elsewhere on the board
/SENSOR_MOSI: U2.32 (PA7); also elsewhere on the board
/SENSOR_SCK: U2.30 (PA5); also elsewhere on the board
/SERVO_CH1_GPIO: U2.81 (PD0); also elsewhere on the board
/SERVO_CH2_GPIO: U2.82 (PD1); also elsewhere on the board
/SWCLK: U2.76 (PA14); also elsewhere on the board
/SWDIO: U2.72 (PA13); also elsewhere on the board
/SWITCH: C43.1, R37.1, U2.88 (PD7)
/VBAT_SENSE: U2.25 (PA2); also elsewhere on the board
/VDD_3V3_RADIO_EN: U2.34 (PC5); also elsewhere on the board
/VDD_3V3_SENSORS_EN: U2.2 (PE3); also elsewhere on the board
/VDD_3V3_STM: C6.2, C8.2, C9.2, C10.2, C11.2, C12.2, C13.2, C14.2, C15.2, J2.4, R3.2, R5.1, R6.1, R7.1, R8.1, R9.1, R38.1, R39.1, U1.3 (~WP), U1.7 (~HOLD), U1.8 (Vdd), U2.11 (VDD), U2.19 (VDD), U2.21 (VREF+), U2.22 (VDDA), U2.28 (VDD), U2.50 (VDD), U2.75 (VDD), U2.100 (VDD), U3.3 (VDD); also elsewhere on the board
/VDD_5V_IN: Q2.2 (S); also elsewhere on the board
/VDD_5V_SENSE: U2.24 (PA1); also elsewhere on the board
/VDD_5V_USB: C1.1, J1.1 (VBUS); also elsewhere on the board
/VDD_BUCK_VALID: U2.91 (PB5); also elsewhere on the board
/VDD_USB_VALID: U2.51 (PB12); also elsewhere on the board
/~RST: U2.14 (NRST), U3.2 (~RST)
GND: C1.2, C2.2, C3.2, C4.1, C5.2, C6.1, C7.2, C8.1, C9.1, C10.1, C11.1, C12.1, C13.1, C14.1, C15.1, C43.2, J1.5 (GND), J2.6, J3.6 (GND), J3.9 (GND), J3.14 (GND), J3.20 (GND), J3.25 (GND), J3.30 (GND), J3.34 (GND), J3.39 (GND), R4.2, R10.2, R27.2, SW1.3 (B), SW1.4 (B), U1.4 (Vss), U2.10 (VSS), U2.20 (VSSA), U2.27 (VSS), U2.74 (VSS), U2.99 (VSS), U3.1 (VSS), Y1.2, Y1.4; also elsewhere on the board
unnamed: C2.1, U2.12 (PH0), Y1.3
unnamed: C3.1, U2.49 (VCAP_1)
unnamed: C4.2, U2.13 (PH1), Y1.1
unnamed: C5.1, U2.73 (VCAP_2)
unnamed: C7.1, D1.1 (K), U2.6 (VBAT)
unnamed: D1.2 (A), R3.1
unnamed: D2.1 (K), J3.2 (5V), J3.4 (5V)
unnamed: D2.2 (A), Q2.3 (D)
unnamed: D8.1 (K), R10.1
unnamed: D9.1 (K), R27.1
unnamed: J1.2 (D-), R1.2
unnamed: J1.3 (D+), R2.2
unnamed: R4.1, U2.94 (BOOT0)
unnamed: R37.2, SW1.1 (A), SW1.2 (A)

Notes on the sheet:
RPI <500mA
STM32 <270mA
STM RESET WATCHDOG
SPI FRAM
BATTERY = VBAT BUCK CONVERTER OUTPUT (VDD_5V_BRICK) = VDD_5V_BUCK USB POWER (VBUS) = VDD_5V_USB RADIO 5V (VDD_5V_RECEIVER) = VDD_5V_RADIO GENERAL 5V (VDD_5V_IN) = VDD_5V_IN TELEM/FRSKY (VDD_5V_PERIPH) = VDD_5V_AUX STM POWER (FMU_VDD_3V3) = VDD_3V3_STM SENSORS POWER (VDD_3V3_SENSORS) = VDD_3V3_SENSO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
VBAT comes in from ESC

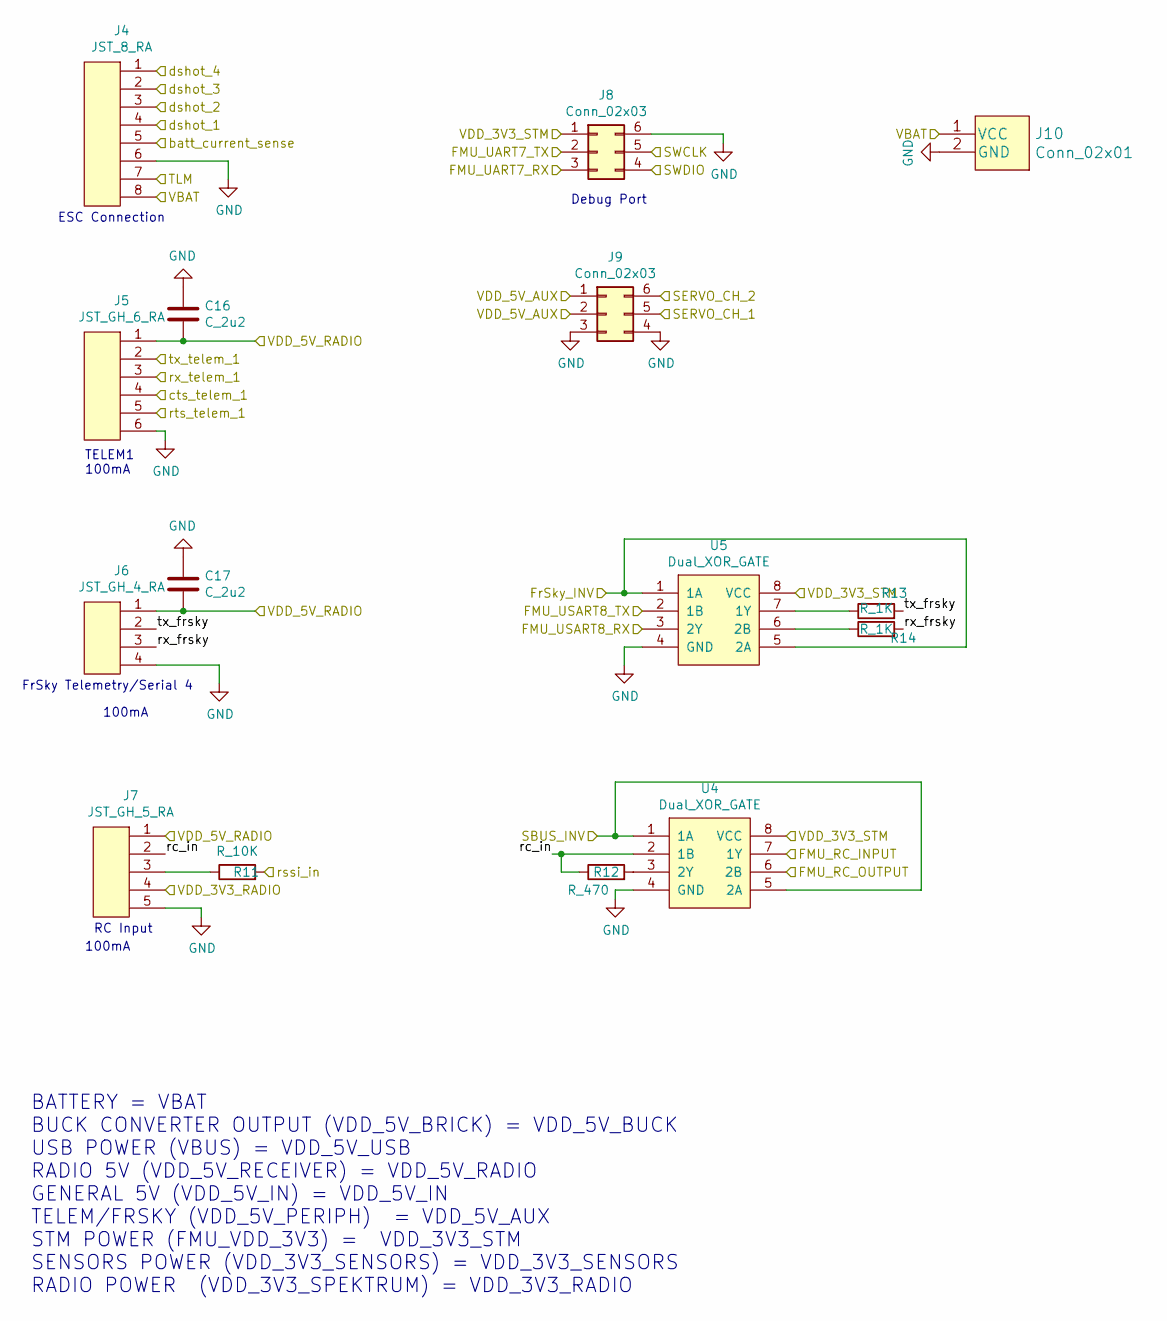
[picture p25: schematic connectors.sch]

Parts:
C16, C17: C_2u2; C_0805
J4: JST_8_RA; JST_SM08B-SRSS-TB(LF)(SN)
J5: JST_GH_6_RA; JST_SM06B-GHS-TB(LF)(SN); MPN SM06B-GHS-TB(LF)(SN)
J6: JST_GH_4_RA; JST_SM04B-GHS-TB(LF)(SN)-; MPN SM04B-GHS-TB(LF)(SN)-
J7: JST_GH_5_RA; SM05B-GHS-TBLFSN; MPN SM05B-GHS-TB(LF)(SN)
J8, J9: Conn_02x03; TSW-103-07-F-D
J10: Conn_02x01; TSW-102-07-F-S
R11: R_10K; R_0805
R12: R_470; R_0805
R13, R14: R_1K; R_0805
U4, U5: Dual_XOR_GATE; TSSOP-8_3x3mm_Pitch0.65mm; MPN 74LVC2G86DP,125

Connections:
/CONNECTORS/rc_in: J7.2, R12.1, U4.2 (1B)
/CONNECTORS/rx_frsky: J6.3, R14.2
/CONNECTORS/tx_frsky: J6.2, R13.2
/ESC_Current_Sense: J4.5; also elsewhere on the board
/ESC_TLM: J4.7; also elsewhere on the board
/FMU_CH1: J4.4; also elsewhere on the board
/FMU_CH2: J4.3; also elsewhere on the board
/FMU_CH3: J4.2; also elsewhere on the board
/FMU_CH4: J4.1; also elsewhere on the board
/FMU_UART7_RX: J8.3; also elsewhere on the board
/FMU_UART7_TX: J8.2; also elsewhere on the board
/FMU_USART2_CTS: J5.4; also elsewhere on the board
/FMU_USART2_RTS: J5.5; also elsewhere on the board
/FMU_USART2_RX: J5.3; also elsewhere on the board
/FMU_USART2_TX: J5.2; also elsewhere on the board
/FMU_USART8_RX: U5.3 (2Y); also elsewhere on the board
/FMU_USART8_TX: U5.2 (1B); also elsewhere on the board
/FrSky_INV: U5.1 (1A), U5.5 (2A); also elsewhere on the board
/RC_INPUT_USART1_RX: U4.7 (1Y); also elsewhere on the board
/RC_OUTPUT_USART1_TX: U4.6 (2B); also elsewhere on the board
/RSSI_IN: R11.2; also elsewhere on the board
/SBUS_INV: U4.1 (1A), U4.5 (2A); also elsewhere on the board
/SERVO_CH1_GPIO: J9.5; also elsewhere on the board
/SERVO_CH2_GPIO: J9.6; also elsewhere on the board
/SWCLK: J8.5; also elsewhere on the board
/SWDIO: J8.4; also elsewhere on the board
/VBAT: J4.8, J10.1 (VCC); also elsewhere on the board
/VDD_3V3_RADIO: J7.4; also elsewhere on the board
/VDD_3V3_STM: J8.1, U4.8 (VCC), U5.8 (VCC); also elsewhere on the board
/VDD_5V_AUX: J9.1, J9.2; also elsewhere on the board
/VDD_5V_RADIO: C16.1, C17.1, J5.1, J6.1, J7.1; also elsewhere on the board
GND: C16.2, C17.2, J4.6, J5.6, J6.4, J7.5, J8.6, J9.3, J9.4, J10.2 (GND), U4.4 (GND), U5.4 (GND); also elsewhere on the board
unnamed: J7.3, R11.1
unnamed: R12.2, U4.3 (2Y)
unnamed: R13.1, U5.7 (1Y)
unnamed: R14.1, U5.6 (2B)

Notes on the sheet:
ESC Connection
Debug Port
TELEM1 100mA
FrSky Telemetry/Serial 4
RC Input
100mA
BATTERY = VBAT BUCK CONVERTER OUTPUT (VDD_5V_BRICK) = VDD_5V_BUCK USB POWER (VBUS) = VDD_5V_USB RADIO 5V (VDD_5V_RECEIVER) = VDD_5V_RADIO GENERAL 5V (VDD_5V_IN) = VDD_5V_IN TELEM/FRSKY (VDD_5V_PERIPH) = VDD_5V_AUX STM POWER (FMU_VDD_3V3) = VDD_3V3_STM SENSORS POWER (VDD_3V3_SENSORS) = VDD_3V3_SENSO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

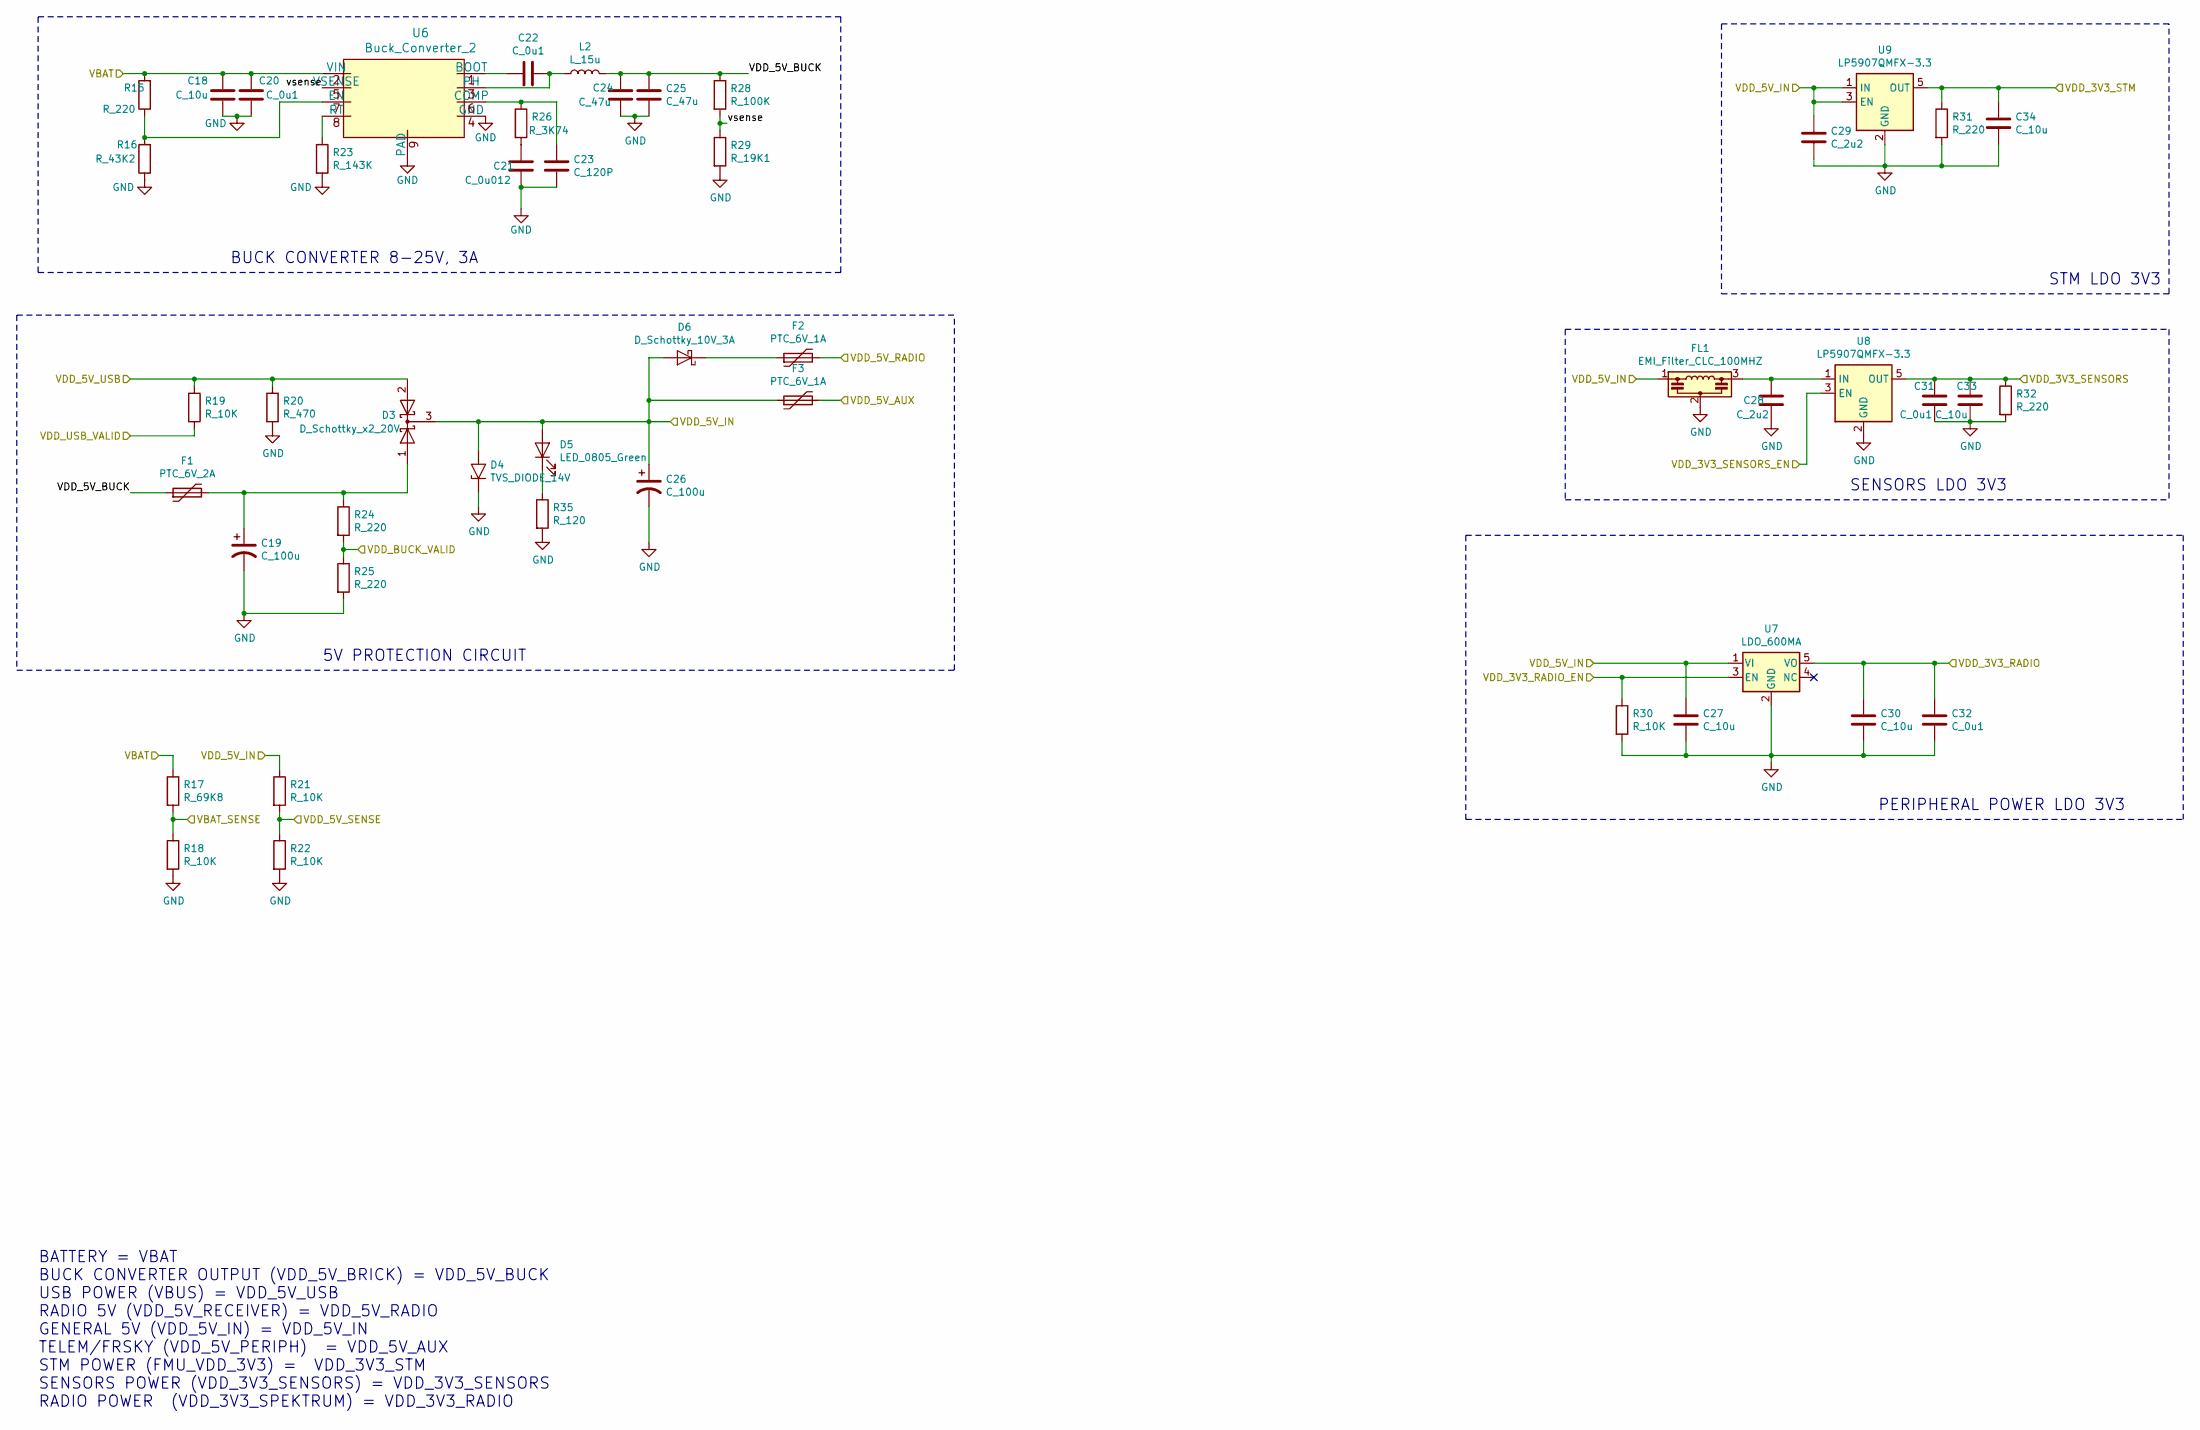
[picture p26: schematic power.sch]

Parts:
C18, C27, C30, C33, C34: C_10u; C_0805
C19, C26: C_100u; 10SGV100M6.3X6.1; MPN 10SGV100M6.3X6.1
C20, C22, C31, C32: C_0u1; C_0805
C21: C_0u012; C_0805; MPN GRM2195C1H123GA01D
C23: C_120P; C_0805; MPN CL21C121JDCNNNC
C24, C25: C_47u; C_0805; MPN JMK212BJ476MG-T
C28, C29: C_2u2; C_0805
D3: D_Schottky_x2_20V; SOT1061; MPN PMEG2020CPA,115
D4: TVS_DIODE_14V; C_0402
D5: LED_0805_Green; LED_0805; MPN LG R971-KN-1
D6: D_Schottky_10V_3A; D_SOD-323F; MPN PMEG1030EJ,115
F1: PTC_6V_2A; Fuse_SMD1206_HandSoldering; MPN 0ZCJ0200FF2C
F2, F3: PTC_6V_1A; R_0805_HandSoldering; MPN 0ZCK0050FF2E
FL1: EMI_Filter_CLC_100MHZ; NFL21SP107X1C3D; MPN NFL21SP107X1C3D
L2: L_15u; 744066150; MPN 744066150
R15, R24, R25, R31, R32: R_220; R_0805
R16: R_43K2; R_0805
R17: R_69K8; R_0805; MPN RC0805FR-0769K8L
R18, R19, R21, R22, R30: R_10K; R_0805
R20: R_470; R_0805
R23: R_143K; R_0805
R26: R_3K74; R_0805; MPN RMCF0805FT3K74
R28: R_100K; R_0805
R29: R_19K1; R_0805; MPN CRCW080519K1FKEA
R35: R_120; R_0805
U6: Buck_Converter_2; TPS54335ADDA; MPN TPS54335ADDA
U7: LDO_600MA; SOT-25_DIO; MPN AP7365-33WG-7
U8, U9: LP5907QMFX-3.3; SOT-23-5; MPN LP5907QMFX-3.3Q1

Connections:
/Power/VDD_5V_BUCK: C24.1, C25.1, F1.1, L2.2, R28.1
/Power/vsense: R28.2, R29.1, U6.5 (VSENSE)
/VBAT: C18.2, C20.1, R15.2, R17.1, U6.2 (VIN); also elsewhere on the board
/VBAT_SENSE: R17.2, R18.1; also elsewhere on the board
/VDD_3V3_RADIO: C30.1, C32.1, U7.5 (VO); also elsewhere on the board
/VDD_3V3_RADIO_EN: R30.1, U7.3 (EN); also elsewhere on the board
/VDD_3V3_SENSORS: C31.1, C33.1, R32.1, U8.5 (OUT); also elsewhere on the board
/VDD_3V3_SENSORS_EN: U8.3 (EN); also elsewhere on the board
/VDD_3V3_STM: C34.1, R31.1, U9.5 (OUT); also elsewhere on the board
/VDD_5V_AUX: F3.2; also elsewhere on the board
/VDD_5V_IN: C26.1, C27.1, C29.1, D3.3 (K), D4.2 (A2), D5.2 (A), D6.2 (A), F3.1, FL1.1, R21.1, U7.1 (VI), U9.1 (IN), U9.3 (EN); also elsewhere on the board
/VDD_5V_RADIO: F2.2; also elsewhere on the board
/VDD_5V_SENSE: R21.2, R22.1; also elsewhere on the board
/VDD_5V_USB: D3.2 (A), R19.1, R20.1; also elsewhere on the board
/VDD_BUCK_VALID: R24.2, R25.1; also elsewhere on the board
/VDD_USB_VALID: R19.2; also elsewhere on the board
GND: C18.1, C19.2, C20.2, C21.2, C23.2, C24.2, C25.2, C26.2, C27.2, C28.2, C29.2, C30.2, C31.2, C32.2, C33.2, C34.2, D4.1 (A1), FL1.2, R16.1, R18.2, R20.2, R22.2, R23.2, R25.2, R29.2, R30.2, R31.2, R32.2, R35.2, U6.4 (GND), U6.9 (PAD), U7.2 (GND), U8.2 (GND), U9.2 (GND); also elsewhere on the board
unnamed: C19.1, D3.1 (A), F1.2, R24.1
unnamed: C21.1, R26.2
unnamed: C22.1, L2.1, U6.3 (PH)
unnamed: C22.2, U6.1 (BOOT)
unnamed: C23.1, R26.1, U6.6 (COMP)
unnamed: C28.1, FL1.3, U8.1 (IN)
unnamed: D5.1 (K), R35.1
unnamed: D6.1 (K), F2.1
unnamed: R15.1, R16.2, U6.7 (EN)
unnamed: R23.1, U6.8 (RT)

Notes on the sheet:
BUCK CONVERTER 8-25V, 3A
STM LDO 3V3
SENSORS LDO 3V3
5V PROTECTION CIRCUIT
PERIPHERAL POWER LDO 3V3
BATTERY = VBAT BUCK CONVERTER OUTPUT (VDD_5V_BRICK) = VDD_5V_BUCK USB POWER (VBUS) = VDD_5V_USB RADIO 5V (VDD_5V_RECEIVER) = VDD_5V_RADIO GENERAL 5V (VDD_5V_IN) = VDD_5V_IN TELEM/FRSKY (VDD_5V_PERIPH) = VDD_5V_AUX STM POWER (FMU_VDD_3V3) = VDD_3V3_STM SENSORS POWER (VDD_3V3_SENSORS) = VDD_3V3_SENSO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

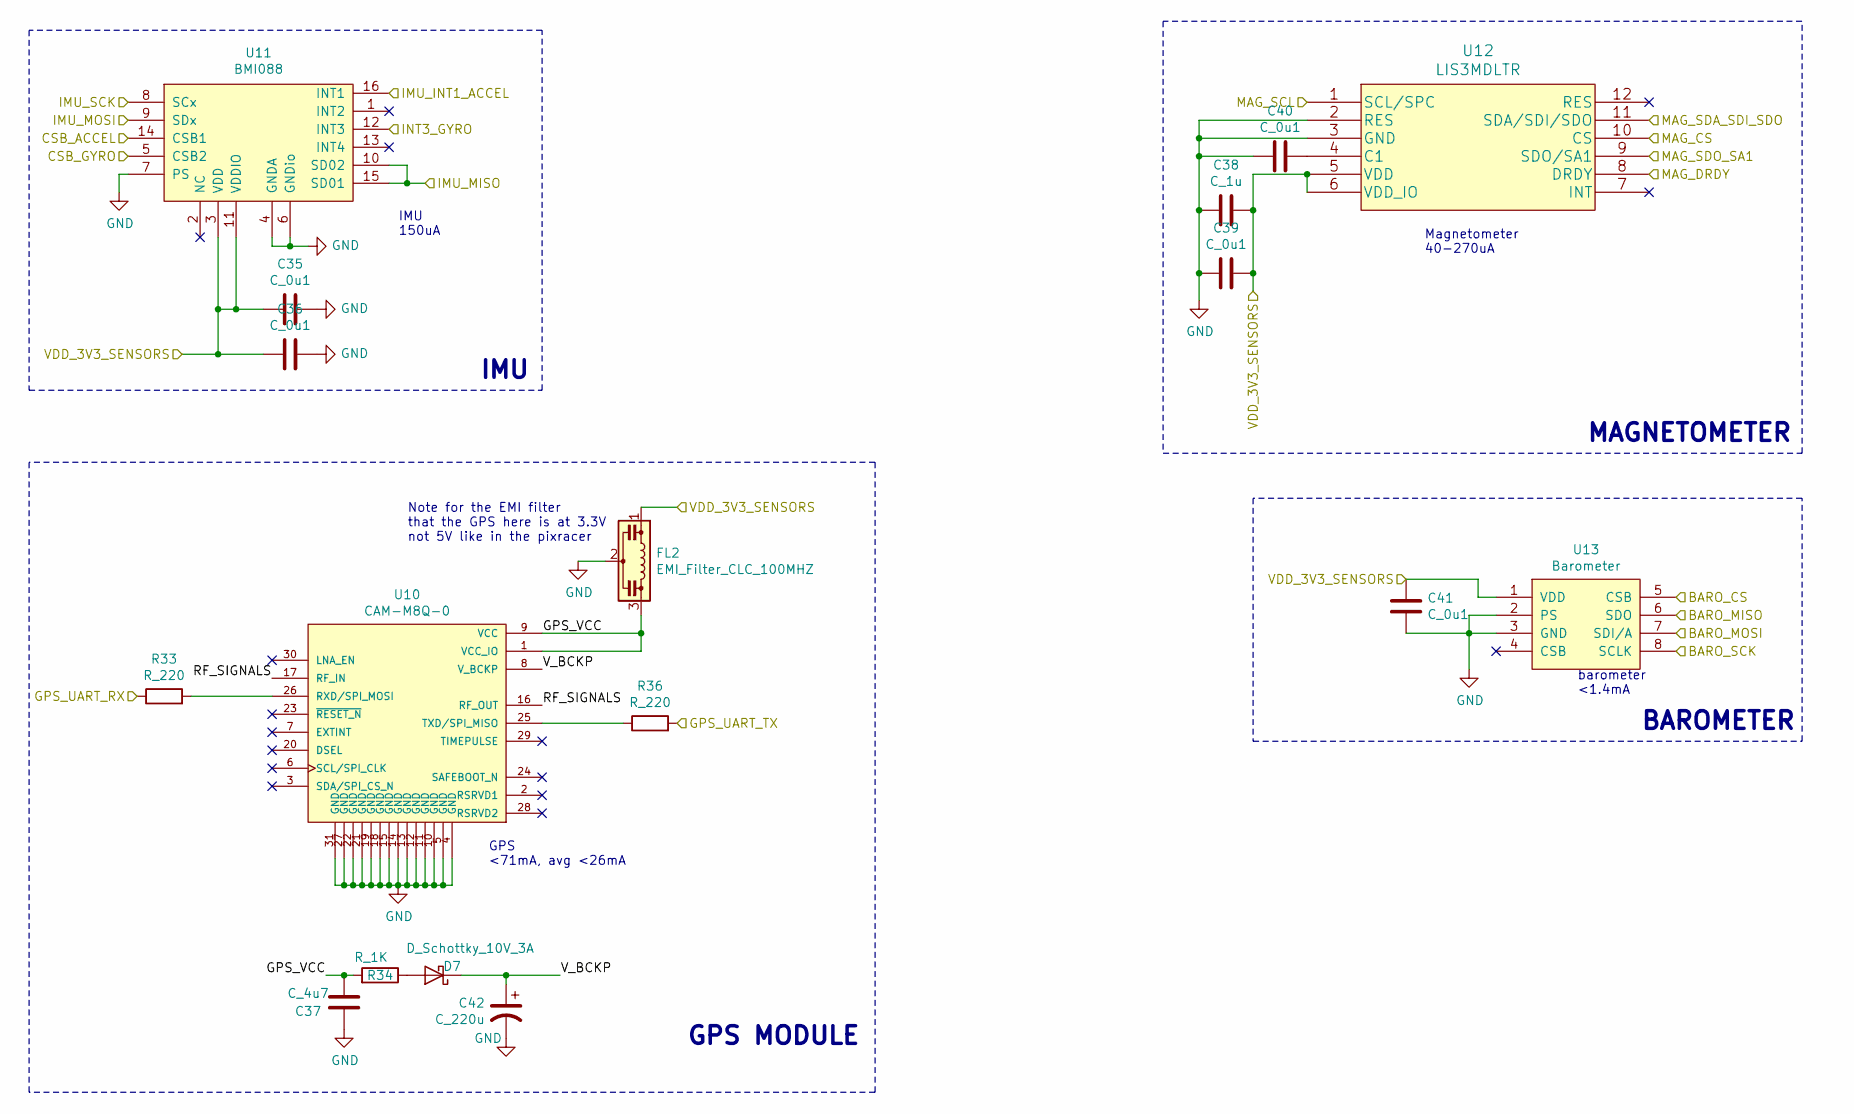
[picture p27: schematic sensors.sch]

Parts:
C35, C36, C39, C40, C41: C_0u1; C_0805
C37: C_4u7; C_0805
C38: C_1u; C_0805
C42: C_220u; UWT0G221MCL6GS; MPN UWT0G221MCL6GS
D7: D_Schottky_10V_3A; D_SOD-323F; MPN PMEG1030EJ,115
FL2: EMI_Filter_CLC_100MHZ; NFL21SP107X1C3D; MPN NFL21SP107X1C3D
R33, R36: R_220; R_0805
R34: R_1K; R_0805
U10: CAM-M8Q-0; CAM_M8Q_0
U11: BMI088
U12: LIS3MDLTR
U13: Barometer; MS561101BA03-50; MPN MS561101BA03-50

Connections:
/ACCEL_DRDY: U11.16 (INT1); also elsewhere on the board
/BARO_CS: U13.5 (CSB); also elsewhere on the board
/GPS_USART6_RX: R33.1; also elsewhere on the board
/GPS_USART6_TX: R36.2; also elsewhere on the board
/GYRO_DRDY: U11.12 (INT3); also elsewhere on the board
/IMU_ACCEL_CS: U11.14 (CSB1); also elsewhere on the board
/IMU_GYRO_CS: U11.5 (CSB2); also elsewhere on the board
/MAG_CS: U12.10 (CS); also elsewhere on the board
/MAG_DRDY: U12.8 (DRDY); also elsewhere on the board
/SENSOR_MISO: U11.10 (SD02), U11.15 (SD01), U12.9 (SDO/SA1), U13.6 (SDO); also elsewhere on the board
/SENSOR_MOSI: U11.9 (SDx), U12.11 (SDA/SDI/SDO), U13.7 (SDI/A); also elsewhere on the board
/SENSOR_SCK: U11.8 (SCx), U12.1 (SCL/SPC), U13.8 (SCLK); also elsewhere on the board
/Sensors/GPS_VCC: C37.2, FL2.3, R34.2, U10.1 (VCC_IO), U10.9 (VCC)
/Sensors/RF_SIGNALS: U10.16 (RF_OUT), U10.17 (RF_IN)
/Sensors/V_BCKP: C42.1, D7.1 (K), U10.8 (V_BCKP)
/VDD_3V3_SENSORS: C35.2, C36.1, C38.1, C39.1, C41.1, FL2.1, U11.3 (VDD), U11.11 (VDDIO), U12.5 (VDD), U12.6 (VDD_IO), U13.1 (VDD); also elsewhere on the board
GND: C35.1, C36.2, C37.1, C38.2, C39.2, C40.2, C41.2, C42.2, FL2.2, U10.4 (GND), U10.5 (GND), U10.10 (GND), U10.11 (GND), U10.12 (GND), U10.13 (GND), U10.14 (GND), U10.15 (GND), U10.18 (GND), U10.19 (GND), U10.21 (GND), U10.22 (GND), U10.27 (GND), U10.31 (GND), U11.4 (GNDA), U11.6 (GNDio), U11.7 (PS), U12.2 (RES), U12.3 (GND), U13.2 (PS), U13.3 (GND); also elsewhere on the board
unnamed: C40.1, U12.4 (C1)
unnamed: D7.2 (A), R34.1
unnamed: R33.2, U10.26 (RXD/SPI_MOSI)
unnamed: R36.1, U10.25 (TXD/SPI_MISO)

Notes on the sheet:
Magnetometer 40-270uA
IMU 150uA
GPS <71mA, avg <26mA
barometer <1.4mA
Note for the EMI filter that the GPS here is at 3.3V not 5V like in the pixracer
GPS MODULE
IMU
MAGNETOMETER
BAROMETER

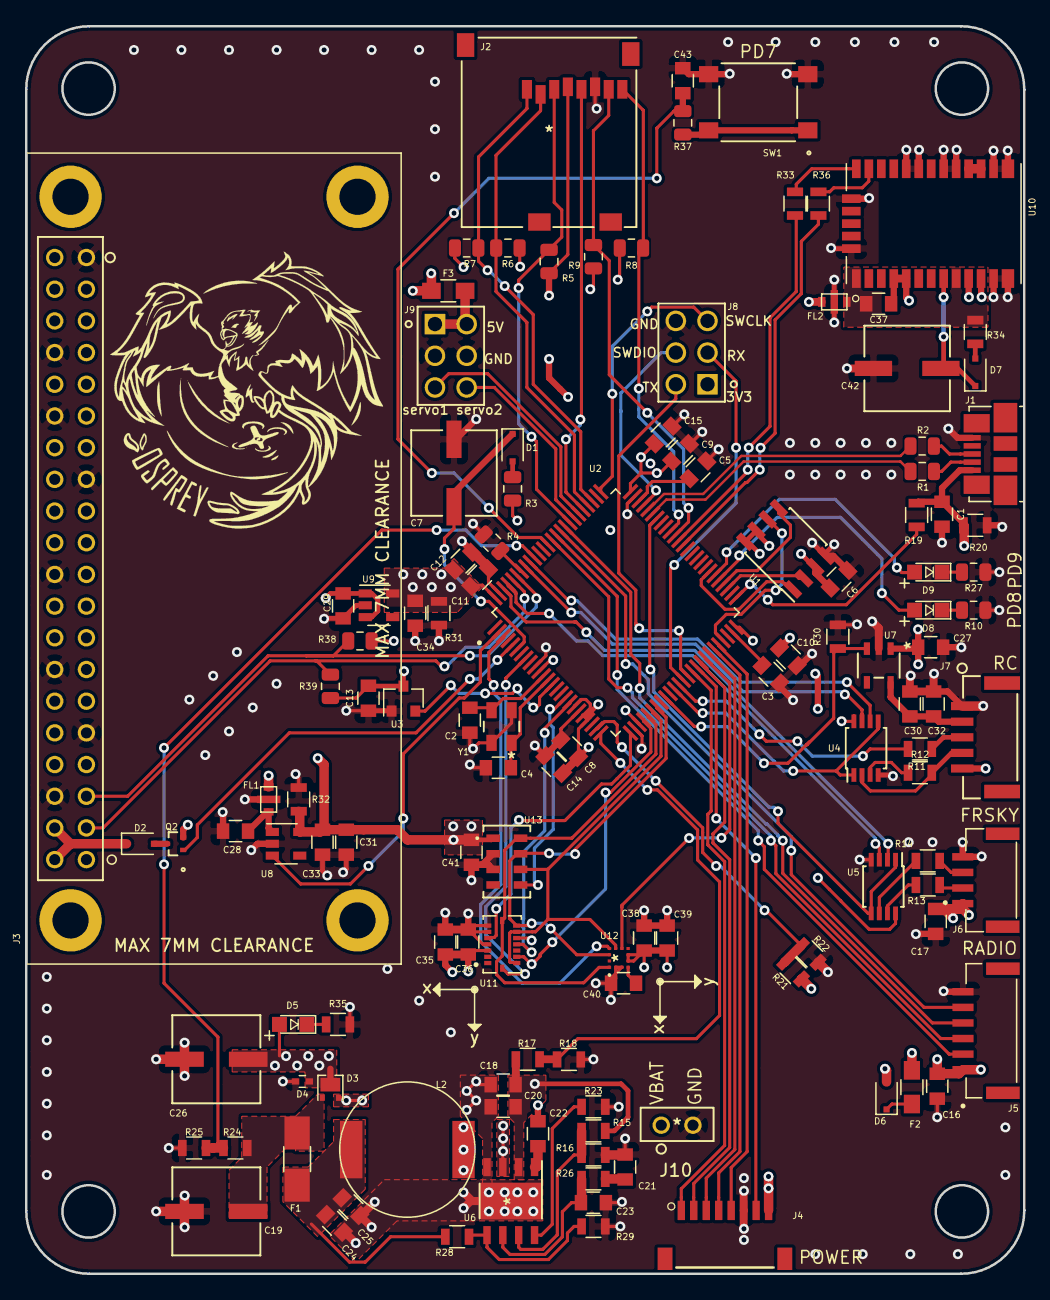
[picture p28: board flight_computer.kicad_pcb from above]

Board: 4 copper layers, 80.0 x 100.0 mm, 123 parts (0 on the bottom side), 109 nets.

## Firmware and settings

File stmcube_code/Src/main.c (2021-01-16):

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

/* Includes ------------------------------------------------------------------*/
#include "main.h"

SPI_HandleTypeDef hspi1;
SPI_HandleTypeDef hspi2;

UART_HandleTypeDef huart7;
UART_HandleTypeDef huart6;

PCD_HandleTypeDef hpcd_USB_OTG_FS;

void SystemClock_Config(void);
static void MX_GPIO_Init(void);
static void MX_SPI1_Init(void);
static void MX_USB_OTG_FS_PCD_Init(void);
static void MX_UART7_Init(void);
static void MX_SPI2_Init(void);
static void MX_USART6_UART_Init(void);
/**
  * @brief  The application entry point.
  * @retval int
  */
int main(void)
{
  /* MCU Configuration--------------------------------------------------------*/

  /* Reset of all peripherals, Initializes the Flash interface and the Systick. */
  HAL_Init();

  /* USER CODE BEGIN Init */
  struct cypress_rdid {
      uint8_t manufacturer[6];
      uint8_t memory;
      uint8_t id1;
      uint8_t id2;
  };

  struct cypress_rdid cyp;
  // const struct cypress_rdid* extra;
  // struct cypress_rdid* extra;

  uint8_t my_rdid[sizeof(cyp)];
  /* USER CODE END Init */

  /* Configure the system clock */
  SystemClock_Config();

  /* Initialize all configured peripherals */
  MX_GPIO_Init();
  MX_SPI1_Init();
  MX_USB_OTG_FS_PCD_Init();
  MX_UART7_Init();
  MX_SPI2_Init();
  MX_USART6_UART_Init();
  /* USER CODE BEGIN 2 */
    // CS pin should default high
  HAL_GPIO_WritePin(GPIOE, GPIO_PIN_4, GPIO_PIN_SET);
  HAL_GPIO_WritePin(GPIOD, GPIO_PIN_10, GPIO_PIN_SET);
  HAL_Delay(100);

  uint8_t device_id[] = {0x7F, 0x7F, 0x7F, 0x7F, 0x7F, 0x7F, 0xC2, 0x21, 0x08};
  uint8_t fram_buf[10];
  uint8_t fram_opcode = 0x9F;
  uint8_t spi_buf = 0x00;
  uint8_t transmit[] = "Still not working...\n\r";
  //write to accel register
  // HAL_GPIO_WritePin(GPIOE, GPIO_PIN_4, GPIO_PIN_RESET);
  // HAL_SPI_Transmit(&hspi1, (uint8_t *)0x0F, 1, 100);
  // HAL_SPI_Receive(&hspi1, &spi_buf, 1, 100);
  // // HAL_Delay(100);
  // // HAL_SPI_Transmit(&hspi1, (uint8_t *)0x7D, 1, 100);
  // // HAL_SPI_Transmit(&hspi1, (uint8_t *)0x04, 1, 100);
  // // HAL_SPI_Receive(&hspi1, &spi_buf, 1, 100);
  // HAL_UART_Transmit(&huart7, &spi_buf, 1, 10);
  // HAL_GPIO_WritePin(GPIOE, GPIO_PIN_4, GPIO_PIN_SET);
  // HAL_Delay(100);
  // HAL_GPIO_WritePin(GPIOD, GPIO_PIN_8, GPIO_PIN_SET);
  // HAL_GPIO_WritePin(GPIOD, GPIO_PIN_9, GPIO_PIN_SET);

  // Say something
  // uart_buf_len = sprintf(uart_buf, "SPI Test\r\n");
  // HAL_UART_Transmit(&huart7, (uint8_t *)uart_buf, uart_buf_len, 100);
  // HAL_UART_Transmit(&huart7, (uint8_t *)uart_buf, uart_buf_len, 100);
  // HAL_UART_Transmit(&huart7, (uint8_t *)uart_buf, uart_buf_len, 100);
  uint8_t who_am_i = (0x0f) | (1 << 7) | (1 << 6);
  char temp[3];
  /* USER CODE END 2 */

  /* Infinite loop */
  /* USER CODE BEGIN WHILE */
  while (1)
  {
  	HAL_Delay(500);
  	HAL_GPIO_WritePin(GPIOE, GPIO_PIN_4, GPIO_PIN_RESET);
    HAL_GPIO_WritePin(GPIOD, GPIO_PIN_10, GPIO_PIN_RESET);
    // HAL_Delay(100);
    // HAL_SPI_Transmit(&hspi1, (uint8_t*)&who_am_i, 1, 100);
    // HAL_SPI_Receive(&hspi1, (uint8_t*)&spi_buf, 1, 100);
    HAL_SPI_TransmitReceive(&hspi1, (uint8_t*)&who_am_i, (uint8_t*)&spi_buf, 2, 100);
    HAL_SPI_TransmitReceive(&hspi2, &fram_opcode, my_rdid, sizeof(my_rdid), 100);
    HAL_GPIO_WritePin(GPIOD, GPIO_PIN_10, GPIO_PIN_SET);
    // HAL_Delay(100);
    HAL_GPIO_WritePin(GPIOE, GPIO_PIN_4, GPIO_PIN_SET);

    const struct cypress_rdid* extra = (const struct cypress_rdid*)my_rdid;
    if (extra->id1 == 0x22) {
      HAL_GPIO_WritePin(GPIOD, GPIO_PIN_8, GPIO_PIN_SET);
      HAL_Delay(1000);
      HAL_GPIO_WritePin(GPIOD, GPIO_PIN_8, GPIO_PIN_RESET);
    }
    // else {
      // transmit[] = "%x"
      // HAL_UART_Transmit(&huart7, &fram_buf[0], 1, 100);
      // HAL_UART_Transmit(&huart7, &device_id[0], 1, 100);
      // HAL_UART_Transmit(&huart7, transmit, 22, 100);
    // }
    // for (int i = 0; i <= 11; i++) {
    //   sprintf(temp, "%x%x%x%x%x%x%x%x\n\r", *device_id);
    // }
    // for (int i = 0; i <= 9; i++) {
    //   sprintf(temp, "%x", *fram_buf);
    //   HAL_UART_Transmit(&huart7, (uint8_t *)temp, 1, 10);
    // }
    sprintf(temp, "%x", extra->id1);
    HAL_UART_Transmit(&huart7, (uint8_t *)temp, 1, 10);
    sprintf(temp, "%x", extra->id2);
    HAL_UART_Transmit(&huart7, (uint8_t *)temp, 1, 10);

    // HAL_UART_Transmit(&huart7, (uint8_t *)temp, 10, 10);
    // transmit[0] = spi_buf;
    // HAL_UART_Transmit(&huart7, transmit, 4, 10);
    // HAL_SPI_Transmit(&hspi1, (uint8_t *)0x29, 1, 100);
    // HAL_SPI_Receive(&hspi1, &spi_buf, 1, 100);
    // transmit[0] = spi_buf;
    // HAL_UART_Transmit(&huart7, transmit, 4, 10);


  	// HAL_Delay(1000);
 //  	uint8_t message[] = "Hi Dan, I'm sentient\n\r";
	// HAL_UART_Transmit(&huart7, message, sizeof(message), 10);
  	HAL_GPIO_WritePin(GPIOD, GPIO_PIN_9, GPIO_PIN_SET);
  	HAL_Delay(500);
  	HAL_GPIO_WritePin(GPIOD, GPIO_PIN_9, GPIO_PIN_RESET);


    /* USER CODE END WHILE */

    /* USER CODE BEGIN 3 */
  }
  /* USER CODE END 3 */
}

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


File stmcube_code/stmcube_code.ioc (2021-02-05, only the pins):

Mcu.UserName=STM32F427VITx
PA1.GPIO_Label=VDD_5V_SENSE
PA1.Signal=ADCx_IN1
PA11.Signal=USB_OTG_FS_DM
PA12.Signal=USB_OTG_FS_DP
PA13.Signal=SYS_JTMS-SWDIO
PA14.Signal=SYS_JTCK-SWCLK
PA2.GPIO_Label=VBAT_SENSE
PA2.Signal=ADCx_IN2
PA3.GPIO_Label=IMU_GYRO_CS
PA3.Signal=GPIO_Output
PA4.GPIO_Label=IMU_ACCEL_CS
PA4.Signal=GPIO_Output
PA5.GPIO_Label=SENSOR_SCK
PA5.Signal=SPI1_SCK
PA6.GPIO_Label=SENSOR_MISO
PA6.Signal=SPI1_MISO
PA7.GPIO_Label=SENSOR_MOSI
PA7.Signal=SPI1_MOSI
PB0.GPIO_Label=ESC_TLM
PB0.Signal=S_TIM3_CH3
PB1.GPIO_Label=ESC_CURRENT_SENSE
PB1.Signal=ADCx_IN9
PB10.Signal=SPI2_SCK
PB12.GPIO_Label=VDD_USB_VALID
PB12.Signal=GPIO_Input
PB14.GPIO_Label=FRAM_MISO
PB14.Signal=SPI2_MISO
PB15.GPIO_Label=FRAM_MOSI
PB15.Signal=SPI2_MOSI
PB5.GPIO_Label=VDD_BUCK_VALID
PB5.Signal=GPIO_Input
PB8.GPIO_Label=RASPI_I2C1_SCL
PB8.Signal=I2C1_SCL
PB9.GPIO_Label=RASPI_I2C1_SDA
PB9.Signal=I2C1_SDA
PC10.Signal=SDIO_D2
PC11.Signal=SDIO_D3
PC12.Signal=SDIO_CK
PC14/OSC32_IN.GPIO_Label=ACCEL_DRDY
PC14/OSC32_IN.Signal=GPIO_Input
PC2.GPIO_Label=BARO_CS
PC2.Signal=GPIO_Output
PC3.GPIO_Label=GYRO_DRDY
PC3.Signal=GPIO_Input
PC6.GPIO_Label=STM_TX_GPS_RX_USART6
PC6.Signal=USART6_TX
PC7.GPIO_Label=STM_RX_GPS_TX_USART6
PC7.Signal=USART6_RX
PC8.Signal=SDIO_D0
PC9.Signal=SDIO_D1
PD0.GPIO_Label=SERVO_CH1
PD0.Signal=GPIO_Output
PD1.GPIO_Label=SERVO_CH2
PD1.Signal=GPIO_Output
PD10.GPIO_Label=FRAM_CS
PD10.Signal=GPIO_Output
PD2.Signal=SDIO_CMD
PD3.GPIO_Label=STM_CTS_TELEM_RTS_USART2
PD3.Signal=USART2_CTS
PD4.GPIO_Label=STM_RTS_TELEM_CTS_USART2
PD4.Signal=USART2_RTS
PD5.GPIO_Label=STM_TX_TELEM_RX_USART2
PD5.Signal=USART2_TX
PD6.GPIO_Label=STM_RX_TELEM_TX_USART2
PD6.Signal=USART2_RX
PD7.GPIO_Label=SWITCH
PD7.Signal=GPIO_Output
PD8.GPIO_Label=DEBUG_LED_1
PD8.Signal=GPIO_Output
PD9.GPIO_Label=DEBUG_LED_2
PD9.Signal=GPIO_Output
PE11.Signal=S_TIM1_CH2
PE12.GPIO_Label=MAG_DRDY
PE12.Signal=GPIO_Input
PE13.Signal=S_TIM1_CH3
PE14.Signal=S_TIM1_CH4
PE3.GPIO_Label=VDD_3V3_SENSORS_EN
PE3.Signal=GPIO_Output
PE4.GPIO_Label=MAG_CS
PE4.Signal=GPIO_Output
PE6.GPIO_Label=RPI_POWER_CTRL
PE6.Signal=GPIO_Output
PE7.GPIO_Label=STM_RX_TELEM_TX_UART7
PE7.Signal=UART7_RX
PE8.GPIO_Label=STM_TX_TELEM_RX_UART7
PE8.Signal=UART7_TX
PE9.Signal=S_TIM1_CH1
PH0/OSC_IN.Signal=RCC_OSC_IN
PH1/OSC_OUT.Signal=RCC_OSC_OUT

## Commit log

2020-09-14 Adds flight computer pcb and parts library start
    [flight_computer.kicad_pcb, flight_computer.sch, sensors.sch]
2020-09-15 Updates flight computer schematics
    [80PIN.sch, FMU_Power.sch, IO.sch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]
2020-09-16 added parts for DAN <3
    [FMU_Power.sch, SD_USB.sch, SERIAL.sch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]
2020-09-20 added more parts and datasheets
    [FMU_Power.sch, SD_USB.sch, SERIAL.sch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]
2020-09-23 Updates SD-USB and SERIAL schematics
    [SD_USB.sch, SERIAL.sch, flight_computer.sch]
2020-10-01 added more parts and 3d files
    [SM04B-GHS-TB(LF)(SN)---3DModel-STEP-56544.STEP, SM06B-GHS-TB(LF)(SN)--3DModel-STEP-56544.STEP]
2020-10-02 added connectors and more components
    [CAM-M8Q-0--3DModel-STEP-56544.STEP, SERIAL.sch, connectors.sch]
2020-10-04 added more components
    [connectors.sch]
2020-10-04 Updates stm to connectors
    [FMU_Power.sch, SD_USB.sch, SERIAL.sch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]
2020-10-04 Adds sensors
    [SD_USB.sch, SERIAL.sch, connectors.sch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]
2020-10-06 Adds more sensor connections and communication with stm
    [SD_USB.sch, connectors.sch, flight_computer.sch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]
2020-10-06 Adds JTAG connections
    [flight_computer.sch]
2020-10-07 Updates drdy pins and rc connections
    [connectors.sch, flight_computer.sch, sensors.sch]
2020-10-07 Adds raspi i2c
    [flight_computer.sch]
2020-10-08 Adds buck converters
    [connectors.sch, flight_computer.sch, sensors.sch]
2020-10-09 Adds in regulators and filters
    [80PIN.sch, FMU_Power.sch, IO.sch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]
2020-10-11 added components, rerranged things to slow down dan
    [SD_USB.sch, connectors.sch, flight_computer.sch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]
2020-10-11 added more components, added buzzer, servo circuits, re-arranged some power
    [SD_USB.sch, connectors.sch, flight_computer.csv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]
2020-10-11 Finishes v1 connections
    [SD_USB.sch, connectors.sch, flight_computer.sch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]
2020-10-11 Adds remainder esc gpio connections
    [flight_computer.sch]
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2020-10-12 Organizes components for layout
    [flight_computer.kicad_pcb, flight_computer.sch]
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2020-10-12 Adds some 3d models
    [CAP_J-V_6P3X6P1_RUB.step, NX3225SA-24_000M-STD-CSR-1_NDK.step, STM32F427VIT6.STEP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]
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2020-10-13 added wider dxf, updated footrprints to show 3D models, adde new dxf to layout and kept old as a dwg in a last ditch attempt to keep the board smaller.
    [circuitBoard v2.dxf, flight_computer.kicad_pcb, sensors.sch]
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2020-10-13 fixed buck converter issue
    [flight_computer.kicad_pcb, power.sch]
2020-10-13 Fits all components on pcb with relative layout
    [flight_computer.kicad_pcb]
2020-10-15 made it a 4 layer board
    [flight_computer.kicad_pcb]
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2020-10-18 Removes buzzer and adds LED pins
    [flight_computer.sch]
2020-10-18 Traces out sensors and additional power lines
    [flight_computer.kicad_pcb]
2020-10-18 more layoutgit add -Agit add -Agit add -Agit add -Agit add -Agit add -Agit add -Agit add -Agit add -Agit add -Agit add -Agit add -Agit add -A
    [flight_computer.kicad_pcb]
2020-10-18 Wires SD card to STM
    [flight_computer.kicad_pcb]
2020-10-19 Wires rpi, gps, and telem
    [flight_computer.kicad_pcb, flight_computer.sch]
2020-10-19 Completes initial v1 pcb traces
    [flight_computer.kicad_pcb, flight_computer.sch]
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2020-10-19 Adds logo to back silk
    [flight_computer.kicad_pcb]
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2020-10-19 added new bom, bad gerber files, and messed with layout
    [flight_computer-B_Cu.gbr, flight_computer-B_Mask.gbr, flight_computer-B_Paste.gbr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]
2020-10-19 Traces out debug LEDs
    [flight_computer.kicad_pcb]
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2020-10-20 Thickens gps power trace and updates servo connector pins
    [connectors.sch, flight_computer.kicad_pcb]
2020-10-20 added switch components, worked on layout. Sensor 3V3 unfinished.
    [flight_computer.kicad_pcb, flight_computer.sch, power.sch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]
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2020-10-20 Adds labels to silkscreen
    [flight_computer.kicad_pcb]
2020-10-20 Adds 2-pin battery connector
    [CON2_1X2_TU_TSW.step, connectors.sch, flight_computer.kicad_pcb]
2020-10-21 fixed BMI088 footprint. Worked on layout
    [flight_computer.kicad_pcb]
2020-10-21 Adds i2c pullup resistors
    [flight_computer.kicad_pcb, flight_computer.sch]
2020-10-22 finished sensor tracing. Added graphics and touched up front silk
    [flight_computer.kicad_pcb]
2020-10-23 added gnd planes to top and bottom
    [flight_computer.kicad_pcb]
2020-10-23 Updates front and back silkscreen
    [flight_computer.kicad_pcb]
2020-10-23 Removes values/references from silk
    [flight_computer.kicad_pcb]
2020-10-23 Updates flight computer rev 1 gerber files
    [flight_computer-B_Cu.gbr, flight_computer-B_Mask.gbr, flight_computer-B_Paste.gbr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]
2020-10-23 fixed issue with plane overlapping. Added new centroid and gerber files
    [flight_computer-B_Cu.gbr, flight_computer-B_Mask.gbr, flight_computer-B_Paste.gbr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]
2020-10-24 fixed issue with RC connector. Try again tomorrow
    [bom_rev1.xlsx, flight_computer.kicad_pcb, sensors.sch]
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2020-10-24 Fixed stm watchdog pinout
    [flight_computer.sch]
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2020-10-24 Fixes watchdog on layout
    [flight_computer.kicad_pcb]
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2020-10-24 added new gerber files
    [flight_computer-B_Cu.gbr, flight_computer-B_Mask.gbr, flight_computer-B_Paste.gbr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]
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2020-10-25 added more 3d components
    [473460001.stp, SM08B-SRSS-TB(LF)(SN)--3DModel-STEP-56544.STEP, csmd-0805_l2-01_w1-25_h1-27.stp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]
2020-10-27 Adds firmware directory and moves files to hardware dir
    [bom_rev1.xlsx, pcbway_bom_rev1.xlsx]
2020-10-27 Prints schematics to pdf and moves board to rev1 folder
    [bom_rev1.xlsx, circuitBoard v1.dxf, circuitBoard v2.dxf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]
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2020-12-06 added sloppy code for spi
    [main.c, stmcube_code.ioc]
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2021-01-16 Removes frysky + spektrum connectors
    [connectors.sch, flight_computer.sch, power.sch]
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2021-01-16 Fix gps uart and update CubeMX config
    [flight_computer.sch]
2021-01-16 Fixes telemetry uart and dshot
    [connectors.sch, flight_computer.sch]
2021-01-23 added new buck converter schematic
    [flight_computer.sch, power.sch]
2021-01-25 added new buck converter
    [power.sch]
2021-02-05 Moves esc current sense to ADC and esc TLM to Timer 3
    [flight_computer.sch]

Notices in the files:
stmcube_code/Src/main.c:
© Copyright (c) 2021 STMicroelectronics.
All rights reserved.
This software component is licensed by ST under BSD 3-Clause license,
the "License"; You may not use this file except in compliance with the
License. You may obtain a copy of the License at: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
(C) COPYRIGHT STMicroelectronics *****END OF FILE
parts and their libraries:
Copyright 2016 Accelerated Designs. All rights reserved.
